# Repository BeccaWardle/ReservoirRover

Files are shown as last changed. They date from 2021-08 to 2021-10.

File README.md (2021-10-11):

# Rover Documentation

This is the documentation for the York University Rover research platform. It is designed to be an expandable platform for robotics research.
It includes:

- [Raspberry Pi 3B+](#raspberry-pi)
- Xilinx Digilent Zybo Z7
- [YDLidar X4](#lidar)
- High Precision AD HAT
- 5x [IR Sensors](#ir-sensors)
  - 3x Sharp GP2Y0A21YK0F (10-80cm)
  - 2x Sharp GP2Y0A41SK0F (4-30cm)
- [Sabertooth 2x12](#motor-driver)
- 4x DC motors
- 4x motor encoders
- 2x 5 Volt regulators

The code is in Python3 on the Raspberry Pi. <br>
One program to record data from the IR and Lidar to the Pi's SD card, another to plot the Lidar and IR data in real time

## Hardware

The focus of my project was focused on using the Lidar and IR sensors for positional processing. <br>
This left several pieces of hardware unused:

- The FPGA chip, which I disconnected from power
- Pi to FPGA connections (left all but pin 12 and 33 connected)
- Motor encoders (completely detatched)

<br>

### System Overview

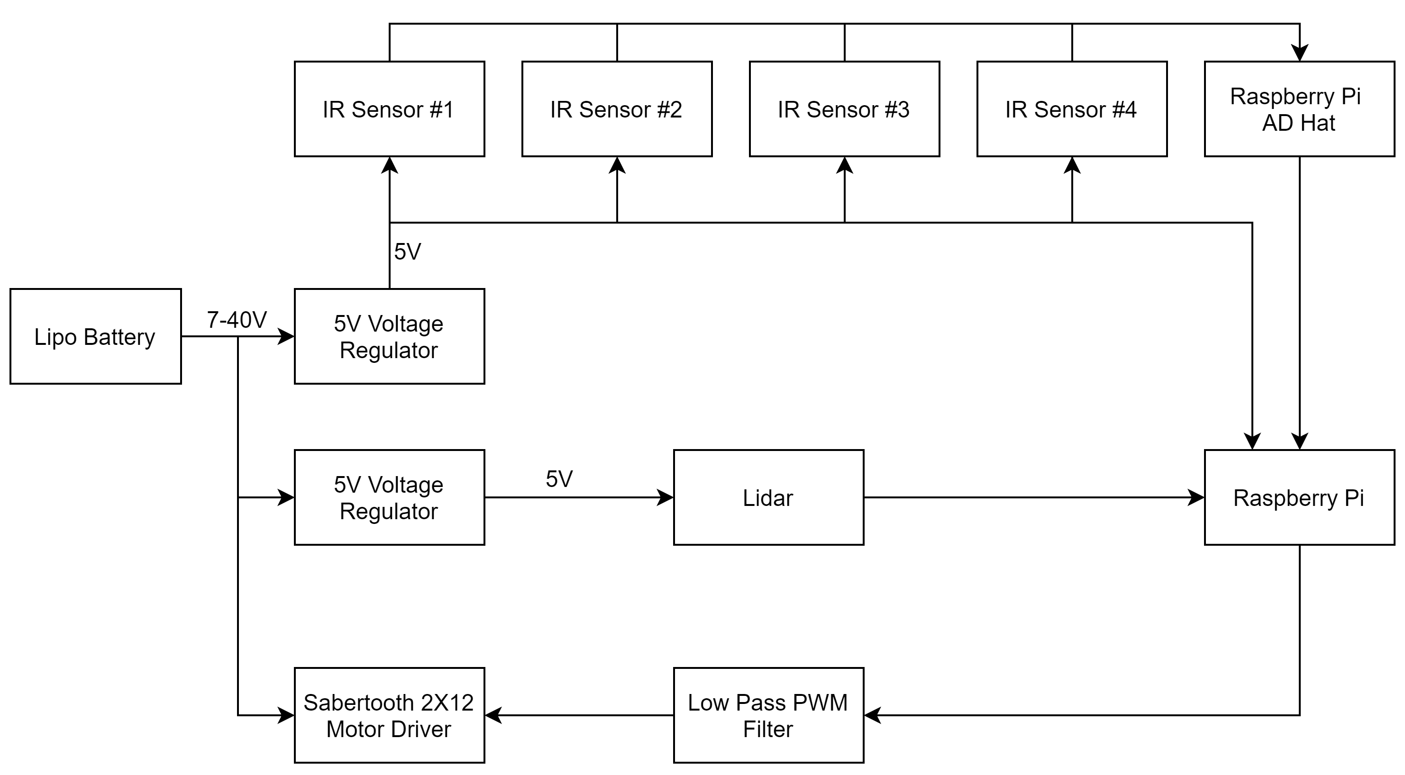
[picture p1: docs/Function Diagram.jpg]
Functional Diagram


As shown in the diagram a (3 cell) lipo battery was used to power the sytem, this was due to issues with the provided UPS. Both the Pi and LIDAR are powered from this via USB cables with stripped ends.

To avoid issues powering both the Lidar and Pi simultanouesly they each have their own a voltage regulator. <br>
One of the regulators (lidar) is connected via the breadboard the other (pi and IR) is connected via red and blue GPIO header cables.

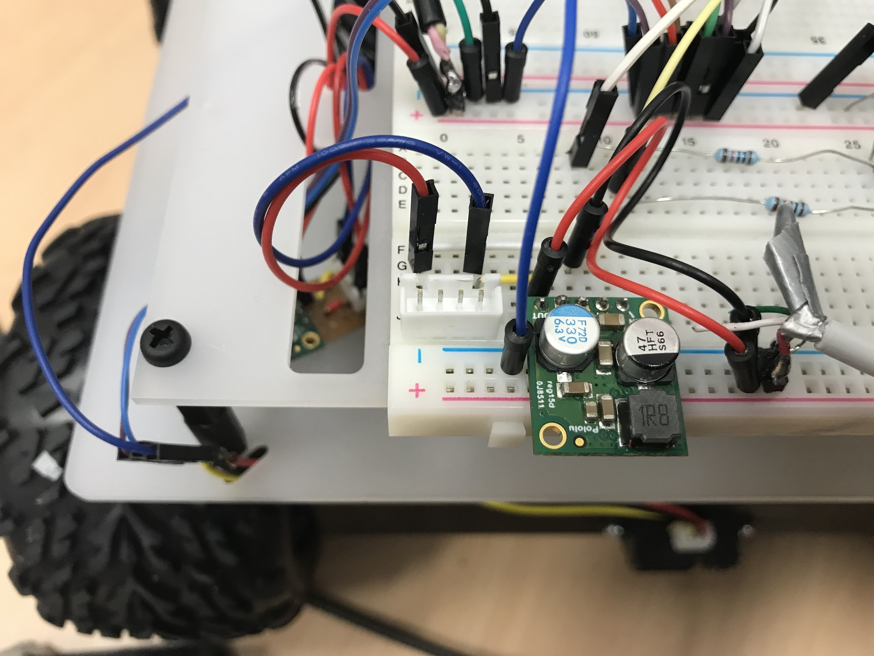
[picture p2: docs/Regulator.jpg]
Regulators


---

### Raspberry Pi

The Raspberry Pi is a model 3B running Raspbian.

The Pi has an HAT which allows it to read the IR sensors.
Most of the GPIO pins on this HAT are connected to the FPGA and are a hold over from an earlier project.
The original FPGA connections are show below

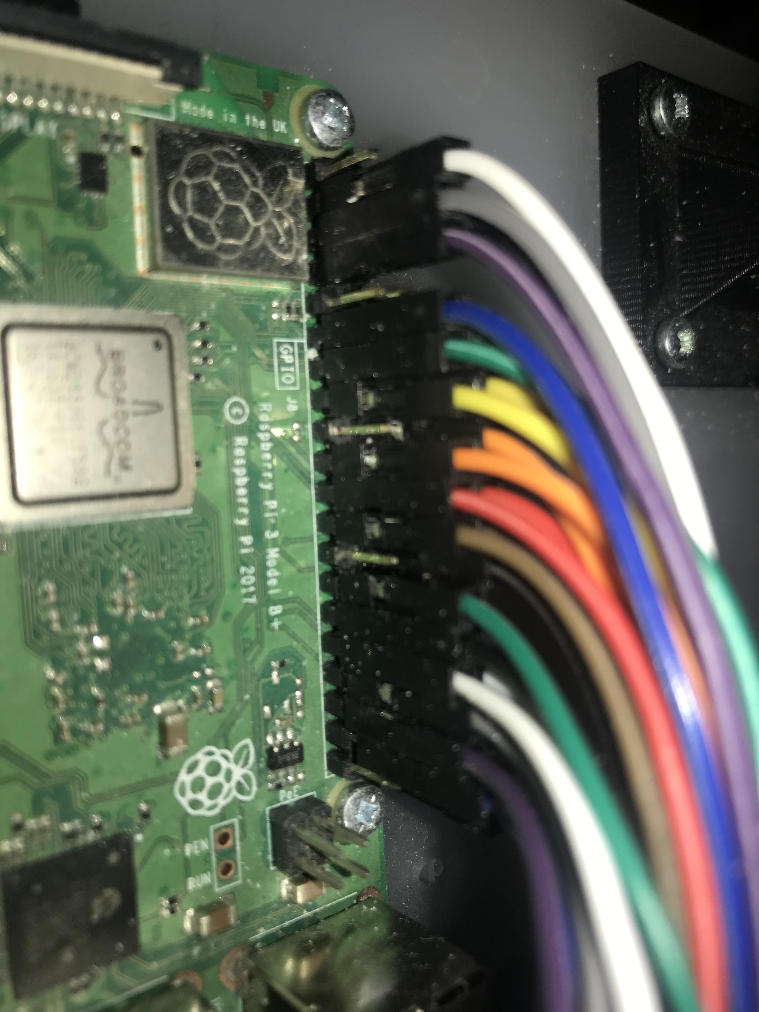
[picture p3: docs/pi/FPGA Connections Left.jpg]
FPGA Connection Left Side

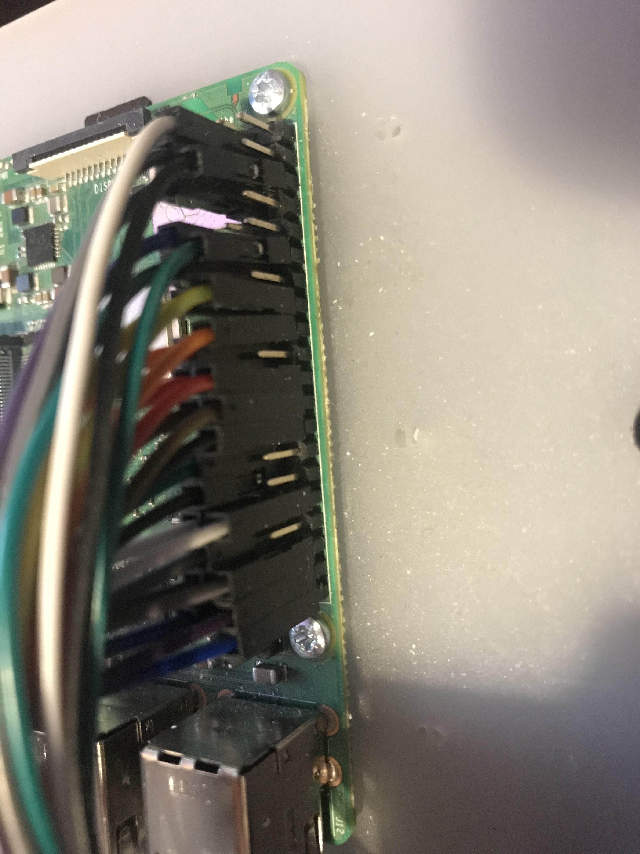
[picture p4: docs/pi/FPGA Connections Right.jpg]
FPGA Connection Right Side


The Pi connected via ground to a common ground shared by all the components.

---

### IR Sensors

The IR sensors are supplied 5V by the same voltage regulator as the Pi via a power rail on the breadboard.

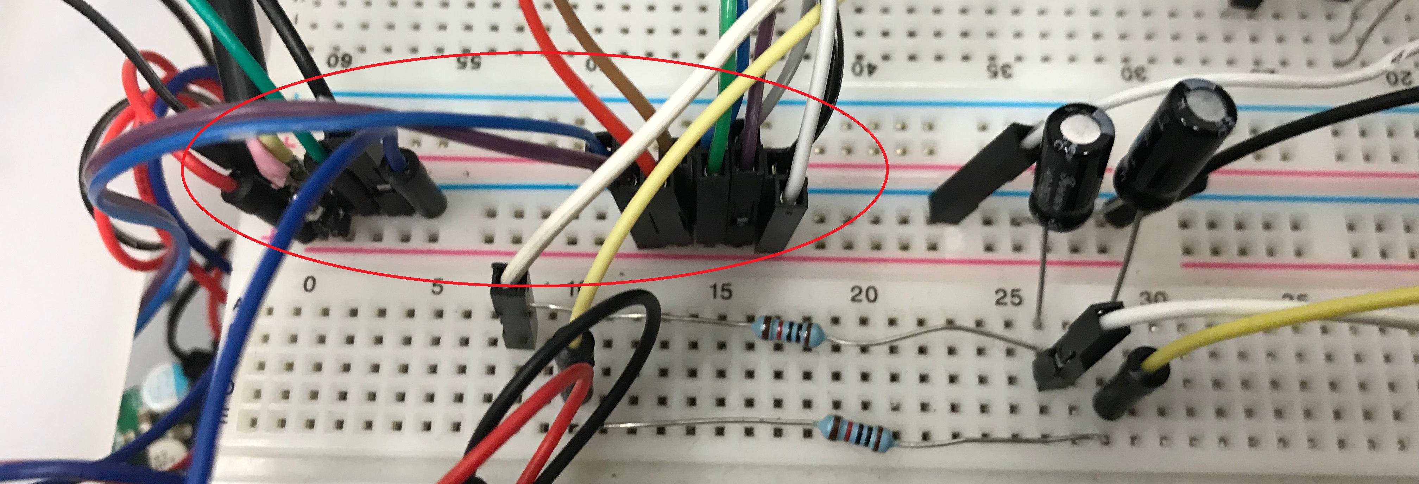
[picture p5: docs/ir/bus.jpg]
IR Power Rail


There are 2 different IR sensors on the vehicle.

- [GP2Y0A21YK0F](https://global.sharp/products/device/lineup/data/pdf/datasheet/gp2y0a21yk_e.pdf) (aka 2Y0A21)
- [GP2Y0A41SK0F](https://global.sharp/products/device/lineup/data/pdf/datasheet/gp2y0a41sk_e.pdf) (aka 0A41SK)

Their outputs vary between the input voltage (5V) and about 0.5V, this is passed into the numbered IN screw terminals on the [High Precision AD HAT](https://www.waveshare.com/wiki/High-Precision_AD_HAT) ([Datasheet](https://www.waveshare.com/w/upload/2/2a/Ads1262.pdf))

Whilst most can be identified by the serial number on their cases some have suffered damage so have been labelled.  

2Y0A21 have a range of 10-80cm <br>
0A41SK have a range of  4-30cm

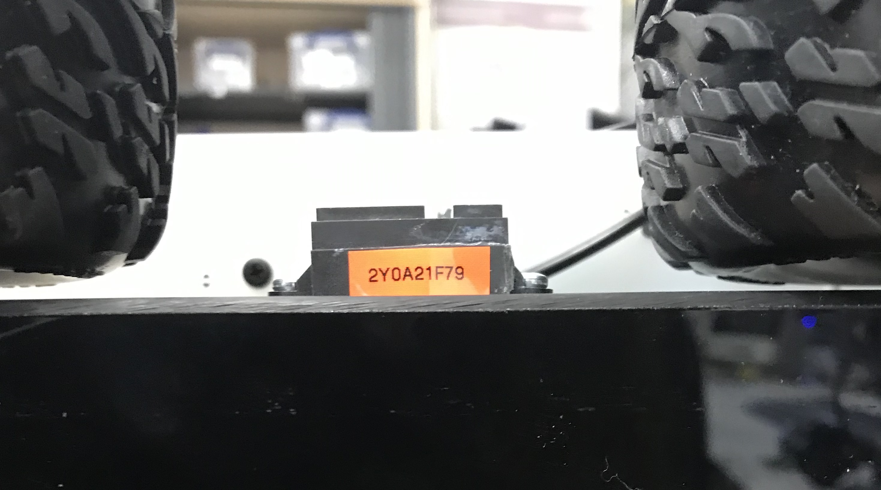
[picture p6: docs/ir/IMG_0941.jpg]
IR Sensor #1

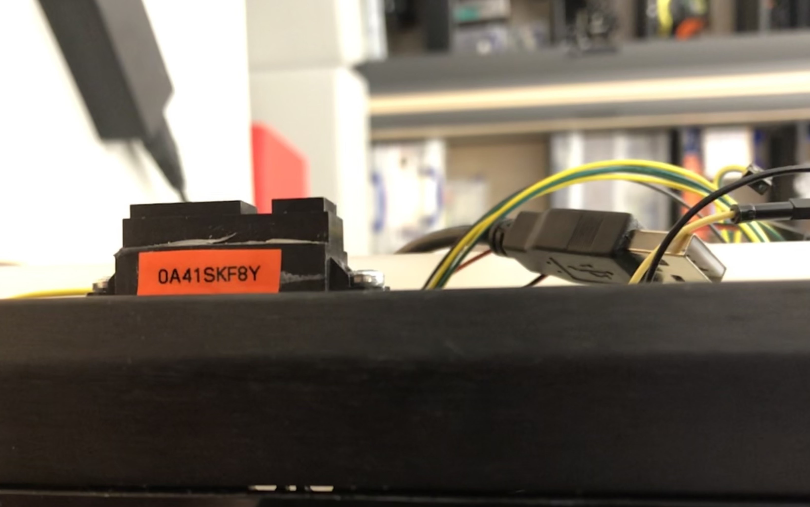
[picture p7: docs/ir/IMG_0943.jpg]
IR Sensor #2

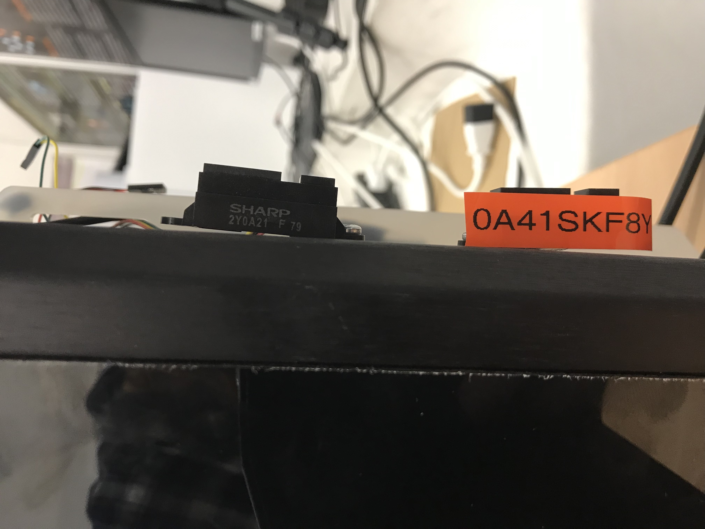
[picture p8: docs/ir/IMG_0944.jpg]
IR Sensor #3

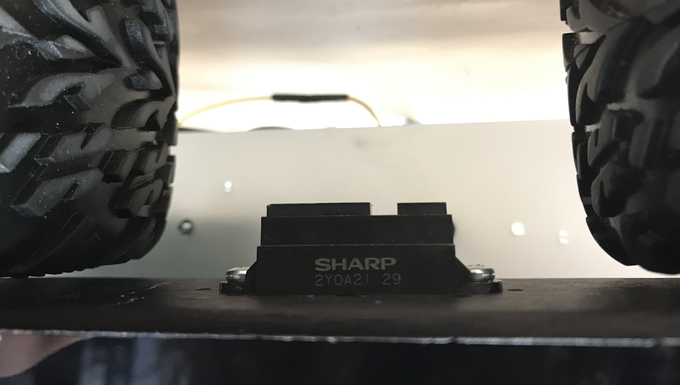
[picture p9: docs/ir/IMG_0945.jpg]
IR Sensor #4

<br><br>
The layout of the IR sensors:<br>
IR layout

Tip:<br>
The IR connectors are coloured red, black and yellow <br>
Red is **data**, *not* live   <br>
Black is **ground** <br>
Yellow is voltage in

---

### LIDAR

The LIDAR is a [YDLIDAR X4](https://www.ydlidar.com/Public/upload/files/2021-08-20/YDLIDAR%20X4%20Data%20sheet%20V2.0.pdf)

Power is provided by seperate 5V regulator to the Pi and IR sensors. This is to avoid voltage spikes that prevented the Lidar motor from spinning up when it's turned on.

The regulator and lidar are both connected via the breadboards' lowest power rail.

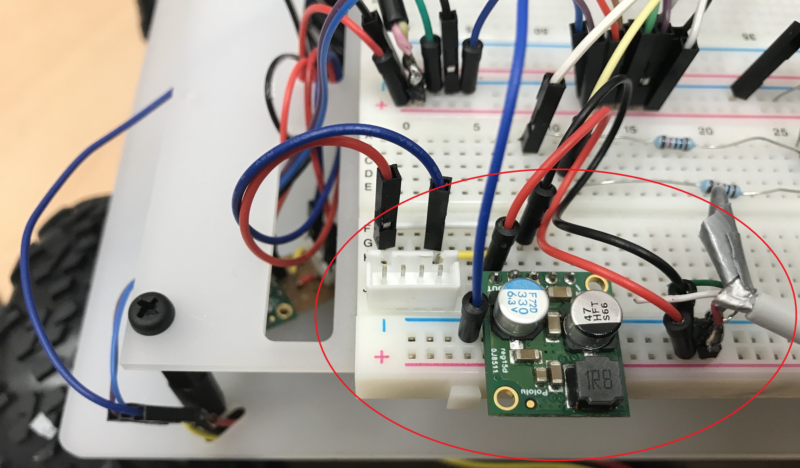
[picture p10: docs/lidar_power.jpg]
Lidar Power


The LIDAR is connected to the Pi via a USB cable.

---

### Motor Driver

The motor driver is a [Sabertooth 2x12](https://www.dimensionengineering.com/datasheets/Sabertooth2x12.pdf)

It is connected to all 4 motors in a tank track configuration

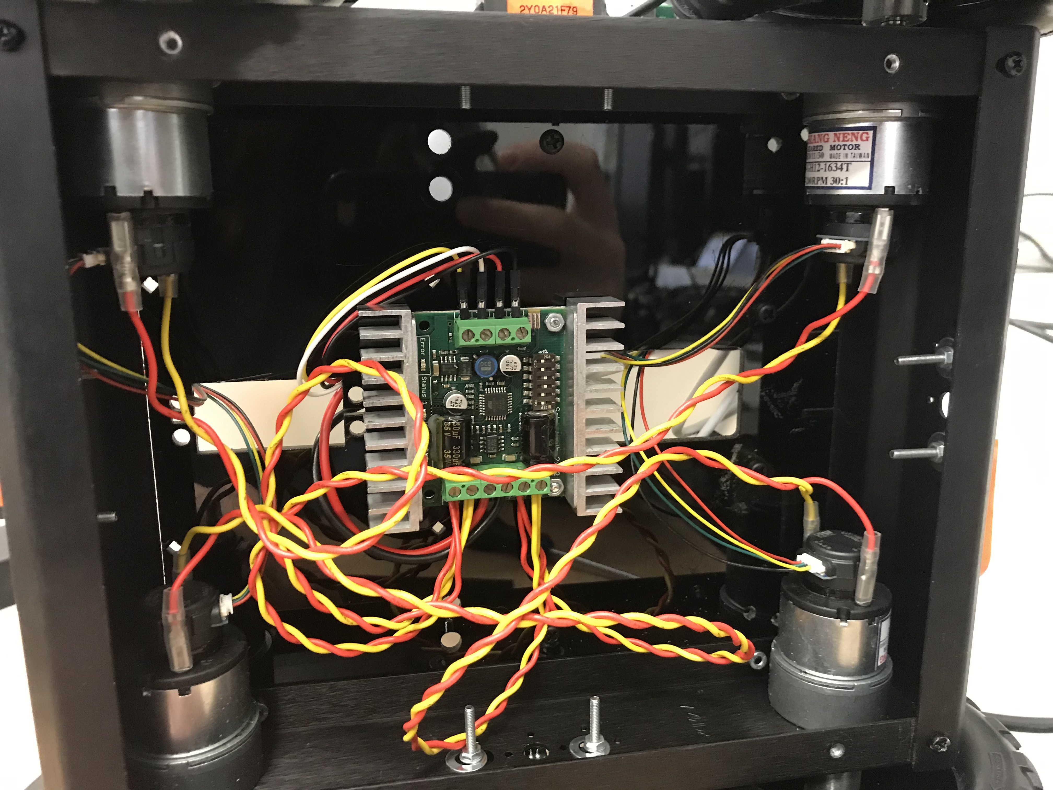
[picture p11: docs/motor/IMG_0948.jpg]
Motor Layout


The motor driver is powered via a battery connector that can be found below the breadboards.

Control is handled by the Pi using pwm. <br>
Pins 12 and 33 are passed into a low pass filter described in the sabertooth documentation

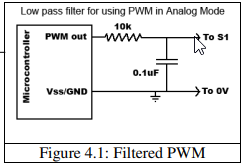
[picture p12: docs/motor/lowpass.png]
Low Pass filter


The Sabertooth settings are controlled by switches on its board. I set them to:<br>
Analogue input with mixed mode, exponential repsonse and 4x sensivity turned off

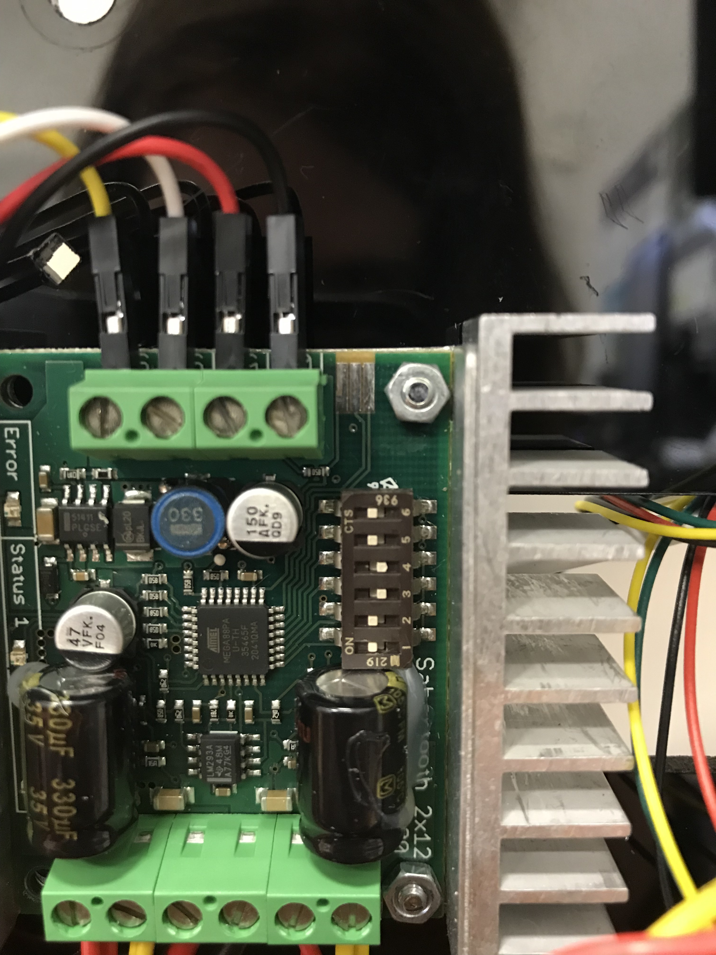
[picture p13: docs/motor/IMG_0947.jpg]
Motor driver settings


Notes:

For some reason a pwm of 80 is stationary, (100 is forward).This means the rover can move much faster backward than forward currently

---

## Software

The software for this project was written in Python 3

The code use <https://github.com/YDLIDAR/YDLidar-SDK> to handle the Lidar and for the HAT some [code](http://www.waveshare.com/w/upload/6/64/High-Pricision_AD_HAT_Code.7z) found on the [waveshare page](https://www.waveshare.com/wiki/High-Precision_AD_HAT) for the HAT (under quick start

Motor control [software](../docs/motor_pwm.py) has been left seperate and minimal

### Lidar

Control of the lidar is done via a Python [API](https://github.com/YDLIDAR/YDLidar-SDK/blob/master/doc/howto/how_to_build_and_install.md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)

It requres `import ydlidar` and then setting the Lidars settings. I found the ones used in this project in the example documentation for the lidar driver

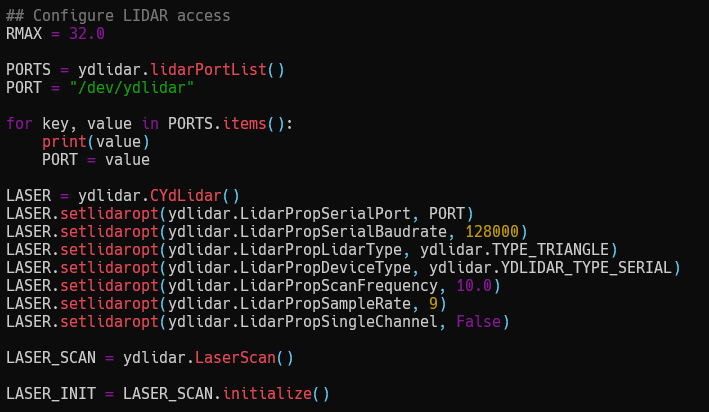
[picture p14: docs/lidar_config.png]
Lidar Settings


The Lidar is turned on

``` python
     # Lidar data
      laser_on = LASER.turnOn()
      if laser_on:
          laser_scan = LASER.doProcessSimple(LASER_SCAN)
          
```

And if successfully turned on, the data (range and corresponding angle) is written into a list

``` python
if laser_scan:
  l_angle = []
  l_range = []
  for point in LASER_SCAN.points:
      l_angle.append(point.angle)
      l_range.append(point.range)
```

### IR and Hat

The output voltage from the IR senors area read into the High Precision AD HAT on the Pi. These values are read as 32 bit signed integers using the [example code](../docs/IR/config.py) which is imported as `ADS1263`

A reference voltage `IR_REF_VOLTAGE` must be set to the voltage of the power rail. 5.08 Volts this setup

After that the readings can be read from the HAT and converted back into voltages and then converted into distances using the code below 

``` python
# IR Data
ir_distances = []
ir_rads = [0.0 ,pi / 2, pi, (3 * pi) / 2]

adc_vales = ADC.ADS1263_GetAll()

for i in range(SENSORS):
    voltage = adc_vales[i] * IR_REF_VOLTAGE / 0x7fffffff

    ir_dist = 29.988 * pow(voltage, -1.173) / 100
    ir_distances.append(ir_dist)
```

### Recording Code

`data_gather.py` is a bare bones data recording file. When run it saves the raw data from the sensors into a file `data/[user name]/[current data and time]` where [user name] is the first argument passed to the program

The angles of the IR sensors are not save automatically and all the voltages are saved as the 32 bit integers read from the HAT with the reference voltage saved above them

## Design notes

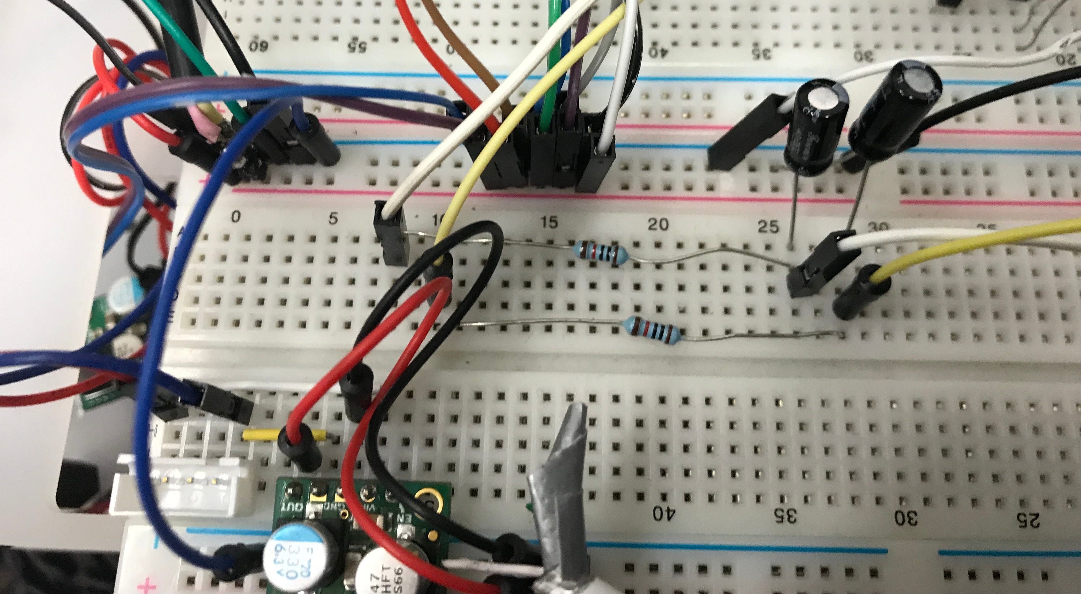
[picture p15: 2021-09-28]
docs/Breadboard.jpg

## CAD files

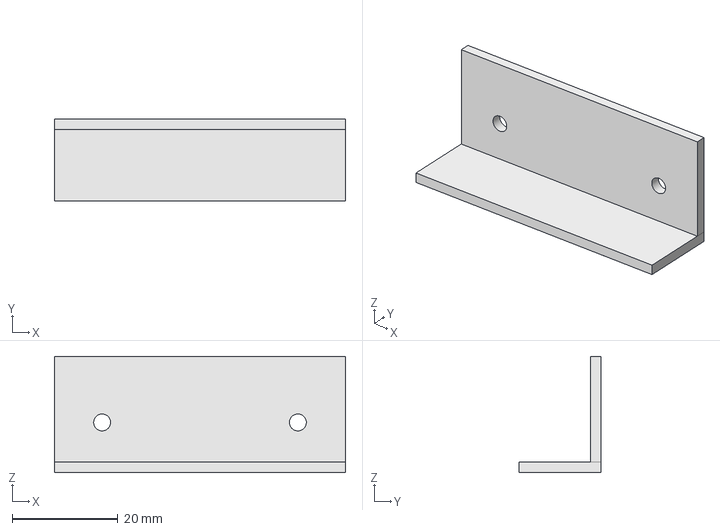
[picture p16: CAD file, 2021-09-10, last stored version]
IR Mount.step
55.0 x 15.5 x 22.0 mm

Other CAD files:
IR Mount.stl
IRMount.FCStd

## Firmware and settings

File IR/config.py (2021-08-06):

# /*****************************************************************************
# * | File        :       config.py
# * | Author      :   Waveshare team
# * | Function    :   Hardware underlying interface
# * | Info        :
# *----------------
# * | This version:   V1.0
# * | Date        :   2020-12-12
# * | Info        :
# ******************************************************************************/
# Permission is hereby granted, free of charge, to any person obtaining a copy
# of this software and associated documnetation files (the "Software"), to deal
# in the Software without restriction, including without limitation the rights
# to use, copy, modify, merge, publish, distribute, sublicense, and/or sell
# copies of the Software, and to permit persons to  whom the Software is
# furished to do so, subject to the following conditions:
#
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

import spidev
import RPi.GPIO as GPIO
import time

# Pin definition
RST_PIN     = 18
CS_PIN      = 22
DRDY_PIN    = 17

# SPI device, bus = 0, device = 0
SPI = spidev.SpiDev(0, 0)

def digital_write(pin, value):
    GPIO.output(pin, value)

def digital_read(pin):
    return GPIO.input(DRDY_PIN)

def delay_ms(delaytime):
    time.sleep(delaytime / 1000.0)

def spi_writebyte(data):
    SPI.writebytes(data)

def spi_readbytes(reg):
    return SPI.readbytes(reg)

def module_init():
    GPIO.setmode(GPIO.BCM)
    GPIO.setwarnings(False)
    GPIO.setup(RST_PIN, GPIO.OUT)
    GPIO.setup(CS_PIN, GPIO.OUT)
    #GPIO.setup(DRDY_PIN, GPIO.IN)
    GPIO.setup(DRDY_PIN, GPIO.IN, pull_up_down=GPIO.PUD_UP)
    SPI.max_speed_hz = 200000
    SPI.mode = 0b01
    return 0;

def module_exit():
    SPI.close()
    GPIO.output(RST_PIN, 0)
    GPIO.output(CS_PIN, 0)
### END OF FILE ###

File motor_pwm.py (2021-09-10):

#!/usr/bin/env python3

import RPi.GPIO as GPIO
from time import sleep

GPIO.setwarnings(False)
GPIO.setmode(GPIO.BOARD)
pin1 = 12
pin2 = 33

GPIO.setup(pin1, GPIO.OUT)
GPIO.setup(pin2, GPIO.OUT)
pin1_pwm = GPIO.PWM(pin1, 1000)
pin2_pwm = GPIO.PWM(pin2, 1000)

pin1_pwm.start(0)
pin2_pwm.start(0)

try:
    while True:
        print("Stay")
        pin1_pwm.ChangeDutyCycle(50)
        pin2_pwm.ChangeDutyCycle(50)
        sleep(1.5)
        print("Forward")
        pin1_pwm.ChangeDutyCycle(100)
        pin2_pwm.ChangeDutyCycle(100)
        sleep(2)
        print("Backward")
        pin1_pwm.ChangeDutyCycle(0)
        pin2_pwm.ChangeDutyCycle(0)
        sleep(2.1)
        print("Turn")
        pin1_pwm.ChangeDutyCycle(100)
        pin2_pwm.ChangeDutyCycle(0)
        sleep(2)
        print("Turn")
        pin1_pwm.ChangeDutyCycle(0)
        pin2_pwm.ChangeDutyCycle(100)
        sleep(2)
        print("Stop")
        pin1_pwm.ChangeDutyCycle(50)
        pin2_pwm.ChangeDutyCycle(50)
        sleep(2)


except KeyboardInterrupt:
    pin1_pwm.stop()
    pin2_pwm.stop()

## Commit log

2021-08-31 Added CAD files of mounting
    [IR Mount.step, IR Mount.stl, IRMount.FCStd]
2021-08-31 Fixed merge conflict
    [IR Mount.step, IR Mount.stl, IRMount.FCStd]
2021-09-10 Intial removal of useless files
    [IR Mount.step, IR Mount.stl, IRMount.FCStd]
